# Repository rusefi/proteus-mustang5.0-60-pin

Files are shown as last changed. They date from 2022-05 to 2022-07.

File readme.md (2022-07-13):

Status: untested

See https://rusefi.com/forum/viewtopic.php?f=2&t=1890

[rev A schematics](https://github.com/rusefi/proteus-mustang5.0-60-pin/blob/main/boards/5.0mustangProteusPnP-a/board/5.0mustangProteusPnP-a-schematic.pdf)

[88 diagram](https://github.com/rusefi/rusefi/wiki/Ford-Fox-Body-(88-Ford-Mustang-302-V8))

# 5.0 Mustang Proteus PnP
PnP adapter board for 5.0 mustang EEC-IV computer using Proteus Rusefi v0.5 compatible board.

This board is designed as both a PnP stock replacement for the A9L/A9P EECs found in 5.0 manual foxbody mustangs, as well as a fully featured aftermarket ECU. This board is designed to fit into BOTH versions of the stock Ford EEC-IV case.

PLEASE do not rip apart any A9L computers to house this unit, there's very few of them left and they sell for a lot! Keep or sell that and buy any late 80s to early 90s EEC-IV as a donor instead such as 88 ford taurus 2.4 EEC for $25.

wiki and more info coming after fully tested.

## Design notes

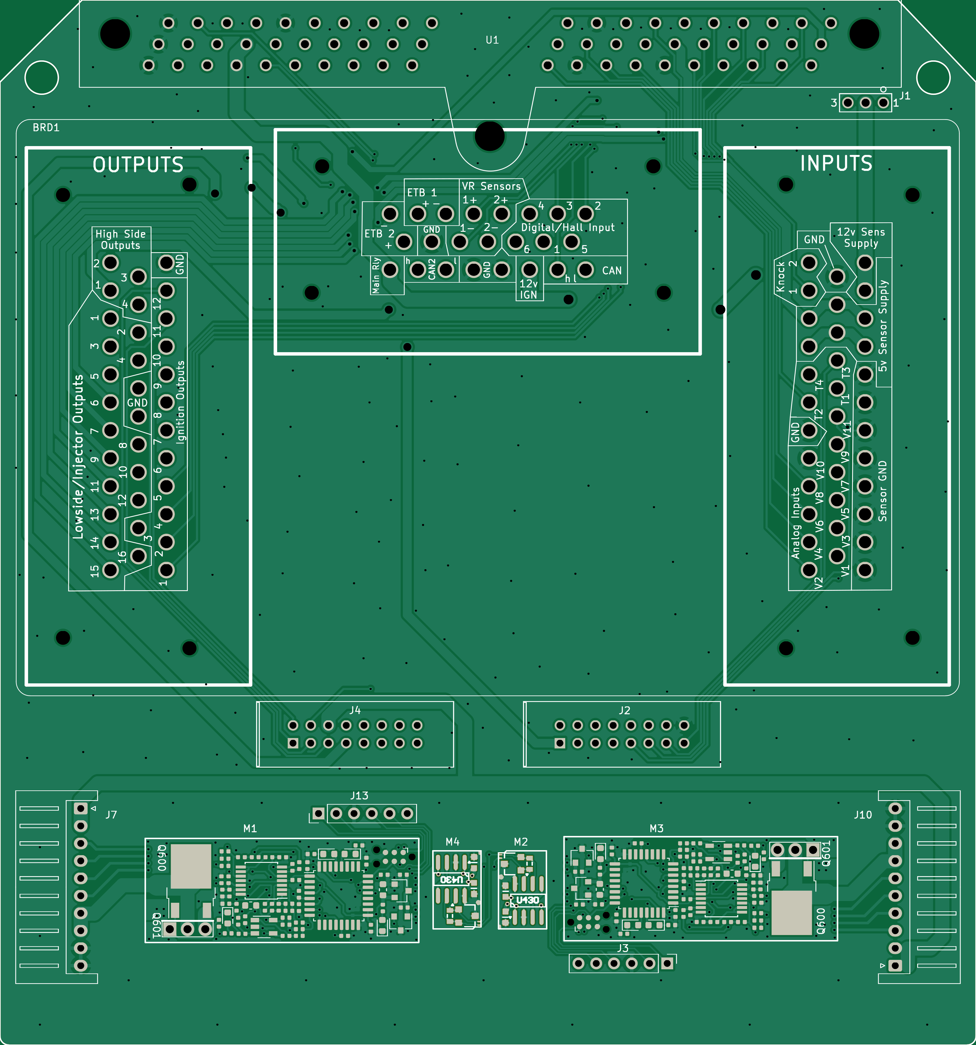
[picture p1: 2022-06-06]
boards/5.0mustangProteusPnP-a/board/misc/5.0mustangProteusPnP-a-top.png

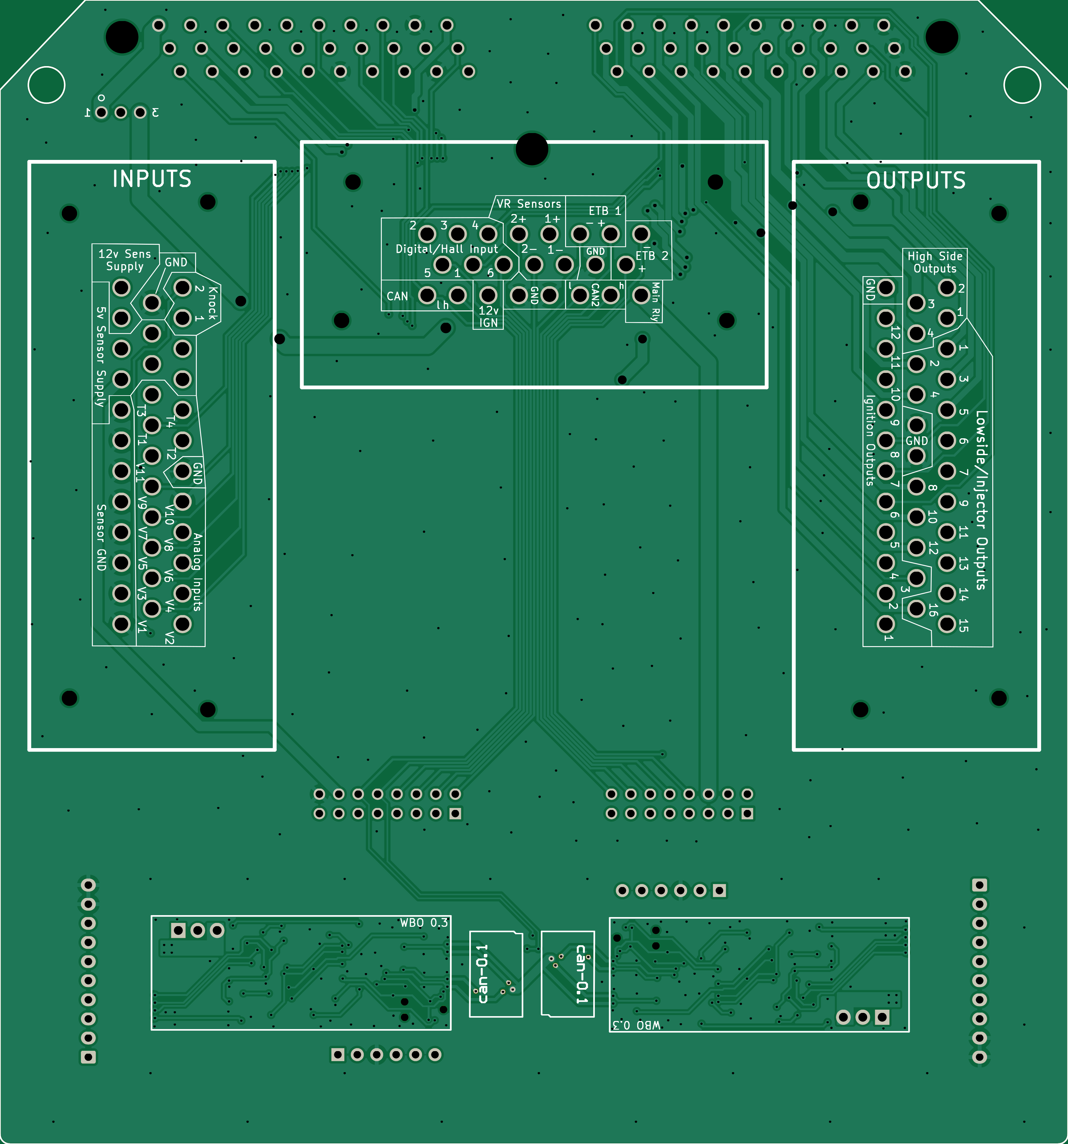
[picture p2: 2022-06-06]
boards/5.0mustangProteusPnP-a/board/misc/5.0mustangProteusPnP-a-bottom.png

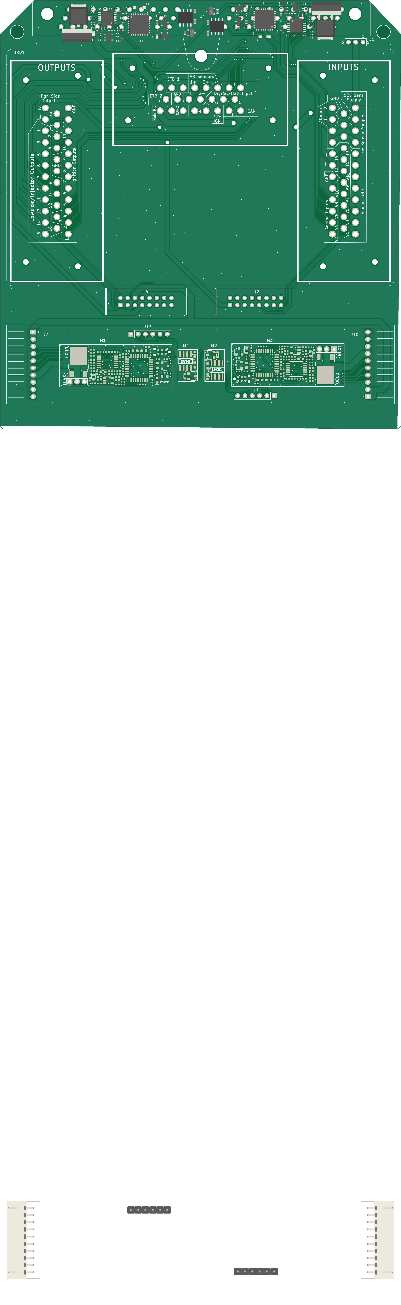
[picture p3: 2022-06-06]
boards/5.0mustangProteusPnP-a/board/5.0mustangProteusPnP-a.png

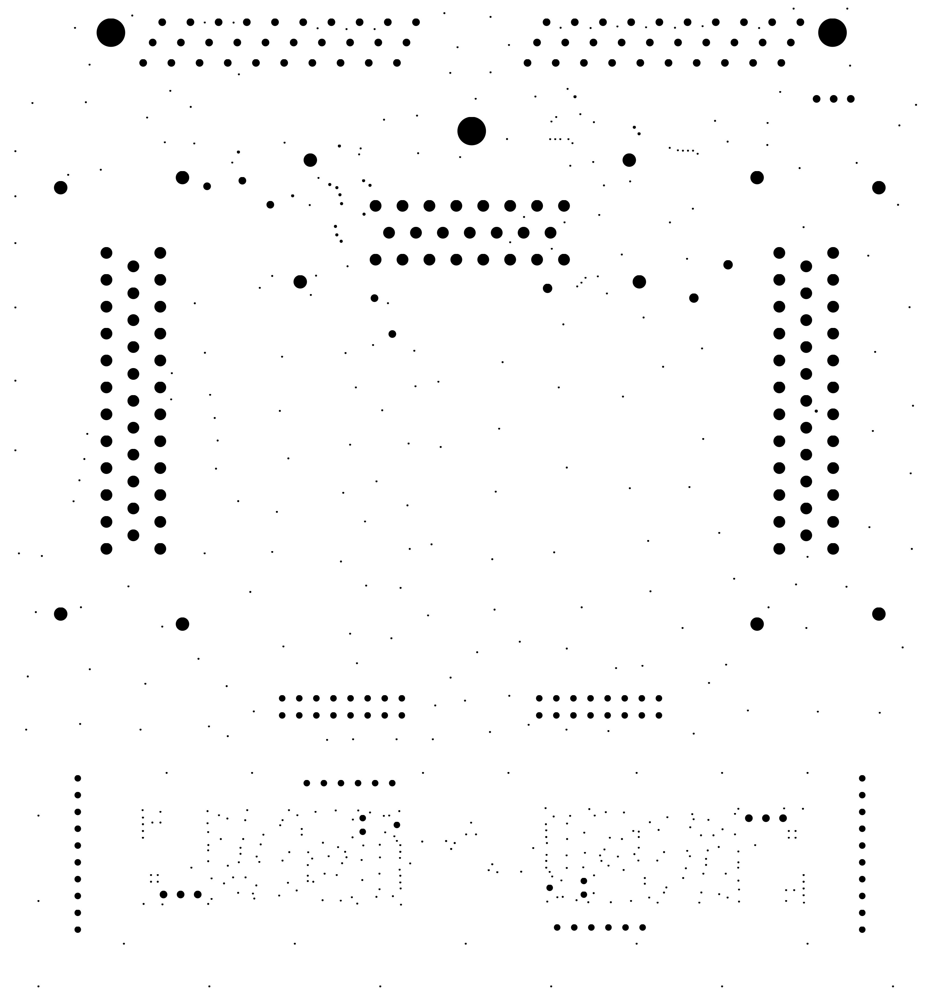
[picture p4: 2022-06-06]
boards/5.0mustangProteusPnP-a/board/misc/5.0mustangProteusPnP-a-outline.png

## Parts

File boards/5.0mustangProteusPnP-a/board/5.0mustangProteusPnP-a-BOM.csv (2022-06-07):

Comment | Designator | Footprint | LCSC Part #
proteus | BRD1 | proteus
5-146280-3 | J1 | 5-146280-3
5103308-3 | J2 | 5103308-3
Conn_01x06 | J3 | PinHeader_1x06_P2.54mm_Vertical
5103308-3 | J4 | 5103308-3
XH-10AW | J7, J10 | JST_XH_S10B-XH-A_1x10_P2.50mm_Horizontal | C14652
Conn_01x06 | J13 | PinHeader_1x06_P2.54mm_Vertical
FORD60PIN | U1 | FORD60PIN
1u | C600, C607, C609, C610, C611, C600_2, C607_2, C609_2, C610_2, C611_2 | C0402 | C52923
100n | C601, C602, C605, C608, C612, C613, C614, C615, C601_2, C602_2, C605_2, C608_2, C612_2, C613_2, C614_2, C615_2 | C0402 | C1525
33n | C603, C603_2 | C0402 | C1585
DNP | C604 | C0402
DNP | C606 | C0402
4.7u | C616, C616_2 | C0603 | C19666
LED-RED-0603 | D600, D603, D600_2, D603_2 | LED-0603 | C2286
LED-GREEN-0603 | D601, D601_2 | LED-0603 | C72043
LED-BLUE-0603 | D602, D602_2 | LED-0603 | C72041
BTS3028 | Q600, Q600_2 | DPAK | C112639
1k | R600, R601, R616, R617, R622, R626, R627, R628, R600_2, R601_2, R616_2, R617_2, R622_2, R626_2, R627_2, R628_2 | R0402 | C11702
68k | R602, R603, R602_2, R603_2 | R0402 | C36871
10k | R604, R605, R613, R614, R618, R619, R625, R604_2, R605_2, R613_2, R614_2, R618_2, R619_2, R625_2 | R0402 | C25744
10 | R606, R606_2 | R0402 | C25077
22k | R607, R607_2 | R0402 | C25768
47 | R608, R608_2 | R0402 | C25118
61.9 | R609, R609_2 | R0603 | C23092
20k | R610, R611, R612, R610_2, R611_2, R612_2 | R0402 | C25765
100k | R615, R621, R615_2, R621_2 | R0402 | C25741
27k | R620, R623, R620_2, R623_2 | R0402 | C25771
3.3k | R624, R624_2 | R0402 | C25890
MCP6004 | U600, U600_2 | TSSOP14 | C50282
STM32F042K6Tx | U602, U602_2 | LQFP32 | C69216
REF3033 | U603, U603_2 | SOT-23 | C36658
XC6206P332MR | U604, U604_2 | SOT-23 | C5446
100n | C430, C431, C430_2, C431_2 | C0603 | C14663
PESD1CAN | D430, D430_2 | SOT-23 | C343993
120 | R430, R430_2 | R0603 | C22787
TJA1051T/3/1J | U430, U430_2 | SO8 | C38695
DNP | C604_2 | C0402
DNP | C606_2 | C0402
GS8331-TR | U601, U601_2 | SOT-23-5 | C157712

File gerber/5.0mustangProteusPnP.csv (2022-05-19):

Comment | Designator | Footprint | LCSC Part #
proteus | BRD1 | Connector_Molex:proteus
5-146280-3 | J1 | 5-146280-3:5-146280-3
5103308-3 | J2 | 51033083:5103308-3
Conn_01x06 | J3 | Connector_PinHeader_2.54mm:PinHeader_1x06_P2.54mm_Vertical
5103308-3 | J4 | 51033083:5103308-3
XH-10AW | J7 | Connector_JST:JST_XH_S10B-XH-A_1x10_P2.50mm_Horizontal | C14652
XH-10AW | J10 | Connector_JST:JST_XH_S10B-XH-A_1x10_P2.50mm_Horizontal | C14652
Conn_01x06 | J13 | Connector_PinHeader_2.54mm:PinHeader_1x06_P2.54mm_Vertical
Module-wbo-0.3 | M1 | hellen-one-wbo-0.3:wbo
Module-can-0.1 | M2 | hellen-one-can-0.1:can
Module-wbo-0.3 | M3 | hellen-one-wbo-0.3:wbo
Module-can-0.1 | M4 | hellen-one-can-0.1:can
FORD60PIN | U1 | FORD60PIN:FORD60PIN

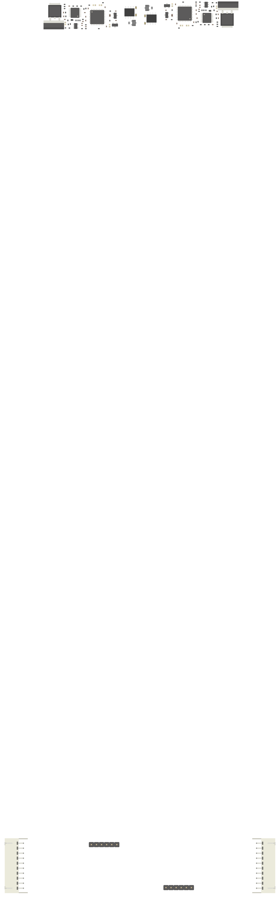
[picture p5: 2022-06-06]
boards/5.0mustangProteusPnP-a/board/misc/5.0mustangProteusPnP-a-components.png

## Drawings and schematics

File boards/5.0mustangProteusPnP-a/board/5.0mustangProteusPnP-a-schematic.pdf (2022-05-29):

# LS15(FAN) A12(1) HS3 A13(23) HS4 A14(22)

# LS4(INJ4) A16(20) GND A17(19) GND A18(18)

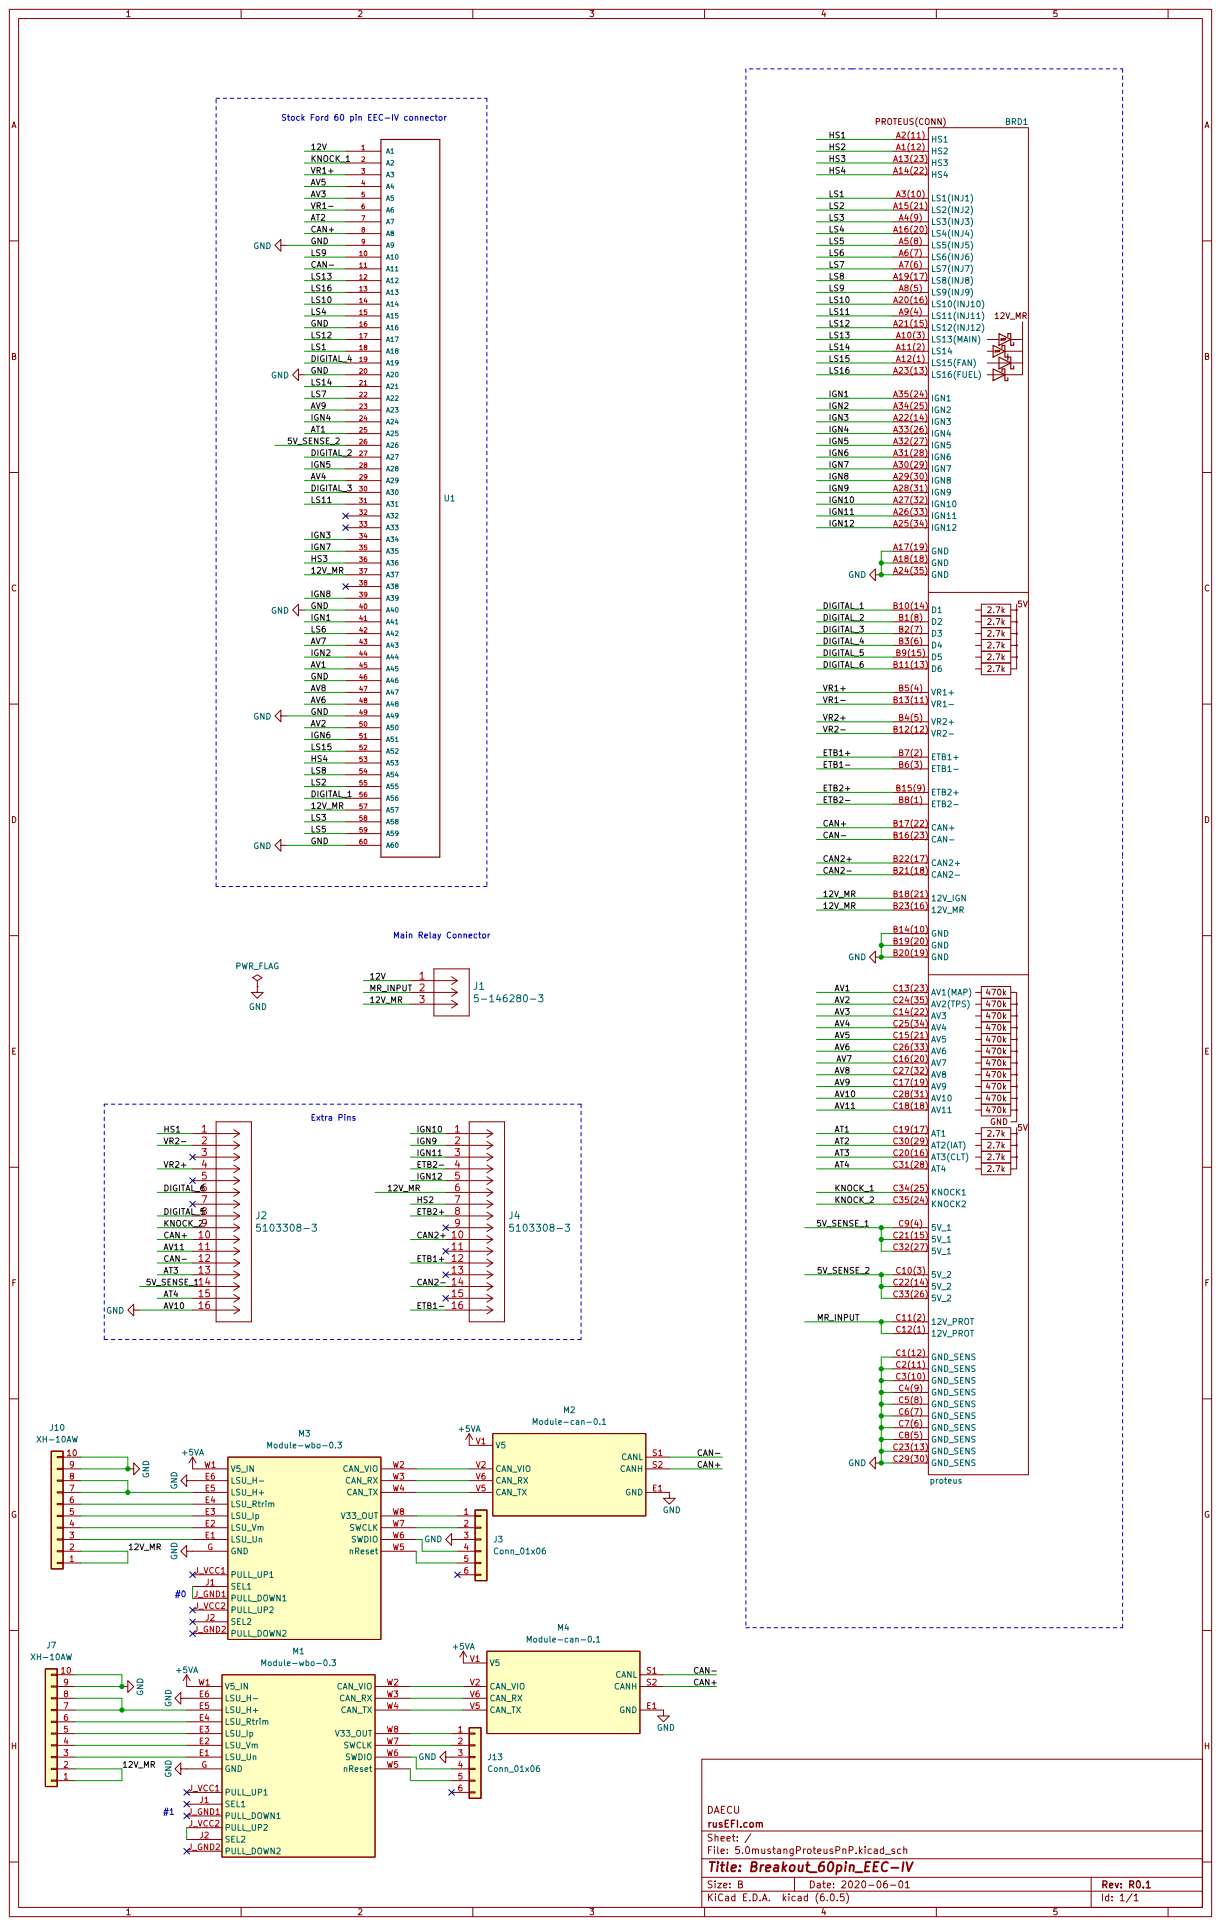
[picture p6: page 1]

IGN10 DIGITAL_2 Main Relay Connector Extra Pins

DAECU
File: 5.0mustangProteusPnP.kicad_sch Sheet: / rusEFI.com

1kR600

3.3k R623

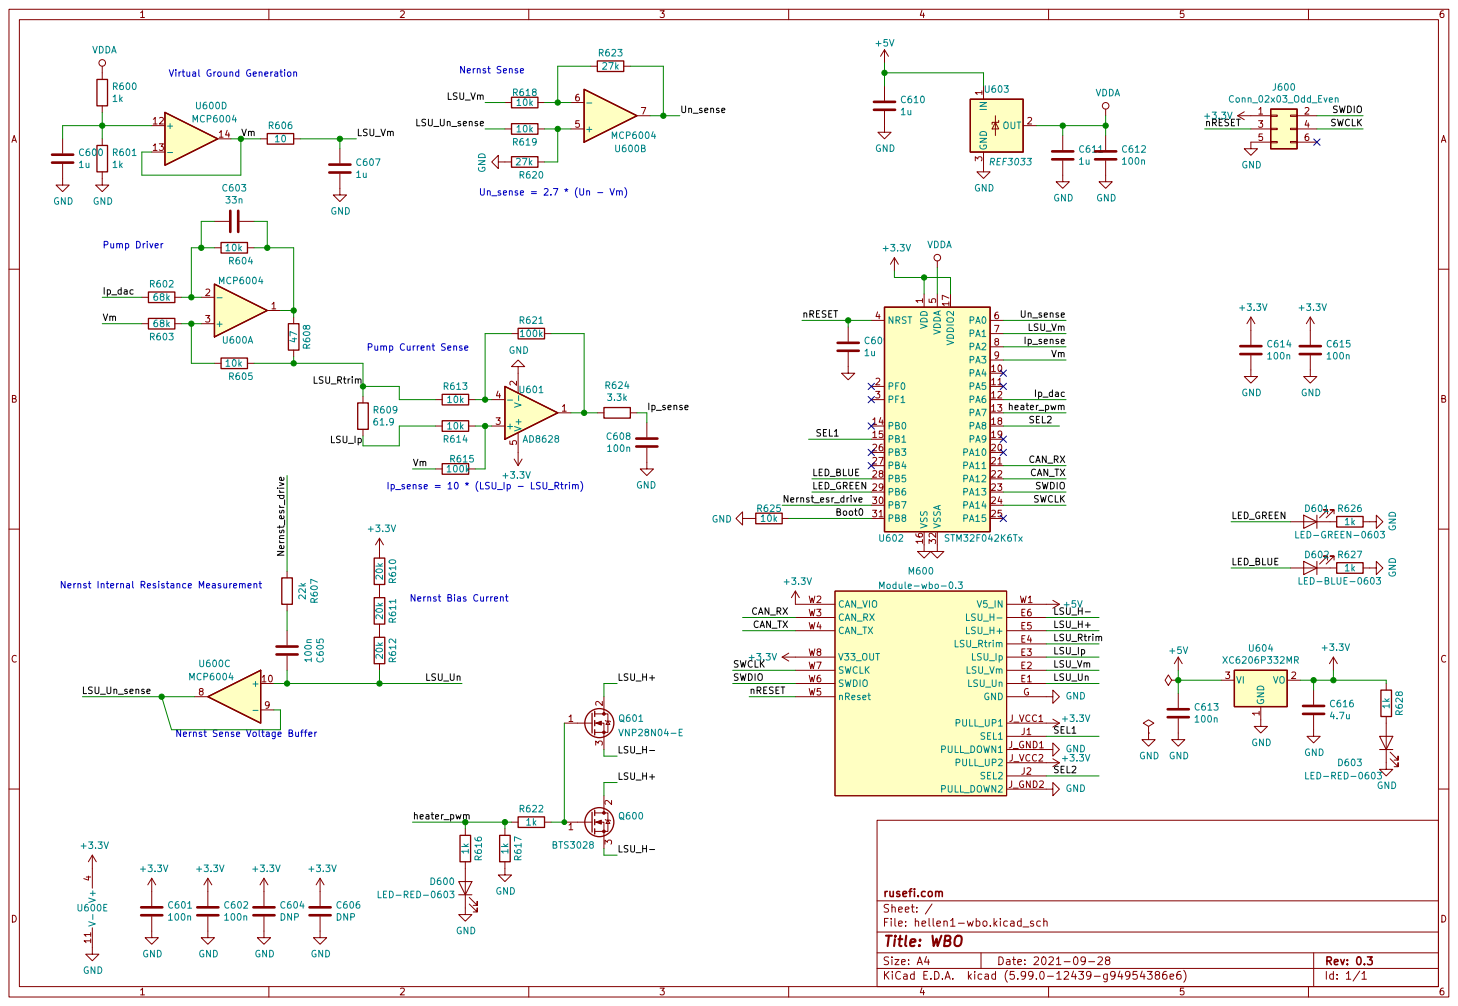
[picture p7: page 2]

Pump Current Sense Nernst Sense

LSU_Vm
Pump Driver Nernst Internal Resistance Measurement

1 VO 2 VI 3 U604 XC6206P332MR GND GND

1 PA4 10 PA5 11 PA6 12 PA7 13 PB0 14 PB1 15 VSS 16 VDDIO2 17 PA8 18 PA9 19 PF0 2 PA10 20 PA11 21 PA12 22 PA13 23 PA14 24 PA15 25 PB3 26 PB4 27 PB5 28 PB6 29 PF1 3 PB7 30 PB8 31 VSSA 32 NRST 4 VDDA

LED-RED-0603 ¹⁰⁰n C⁶⁰⁵ C604 DNP

Nernst Sense Voltage Buffer

1k GND GND R⁶¹⁶ ¹k

File: hellen1-wbo.kicad_sch Sheet: / rusefi.com

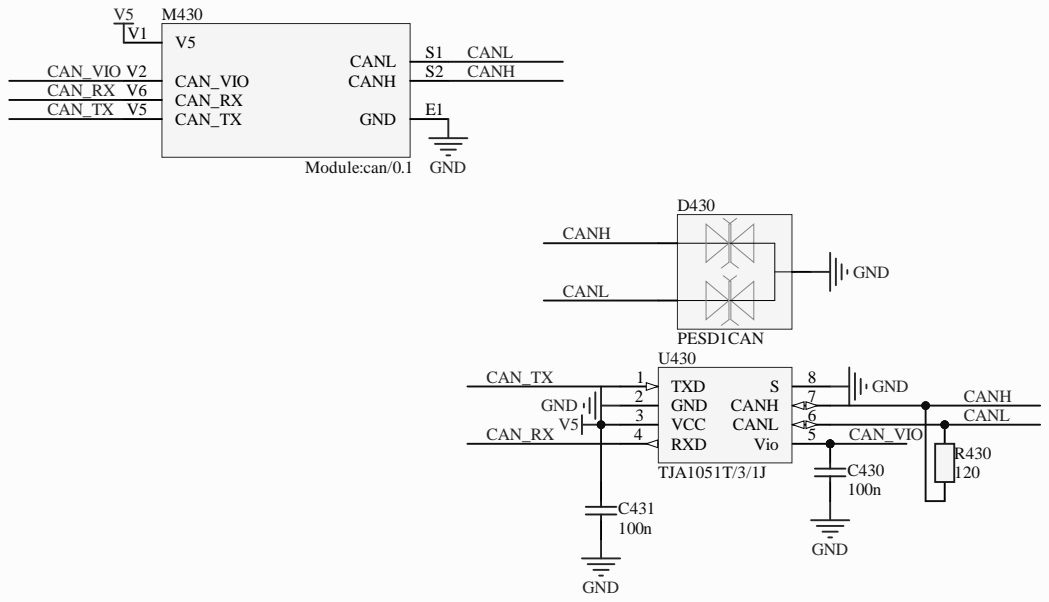
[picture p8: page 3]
andreika; Size:; Author:; Date:; Revision:; Sheet; PESD1CAN; GND; CANH; CANL; TXD 1 GND 2 VCC 3; Vio; 5 RXD 4; 6 CANH; TJA1051T/3/1J; CANH CANL; CAN_TX; CAN_RX; CAN_VIO; CAN_VIO V2; S2 CANL; CAN_TX V5; CAN_RX V6; Module:can/0.1

Hellen-One CAN
Title:

rusEFI EMS
Hellen-One Platform
https://rusefi.com/s/hellen72

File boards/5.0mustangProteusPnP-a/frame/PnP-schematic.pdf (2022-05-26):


IGN10 DIGITAL_2 Main Relay Connector Extra Pins

4 | LSU_Vm E2 | 2
3 | LSU_Un E1 | 3

DAECU
File: 5.0mustangProteusPnP.kicad_sch Sheet: / rusEFI.com

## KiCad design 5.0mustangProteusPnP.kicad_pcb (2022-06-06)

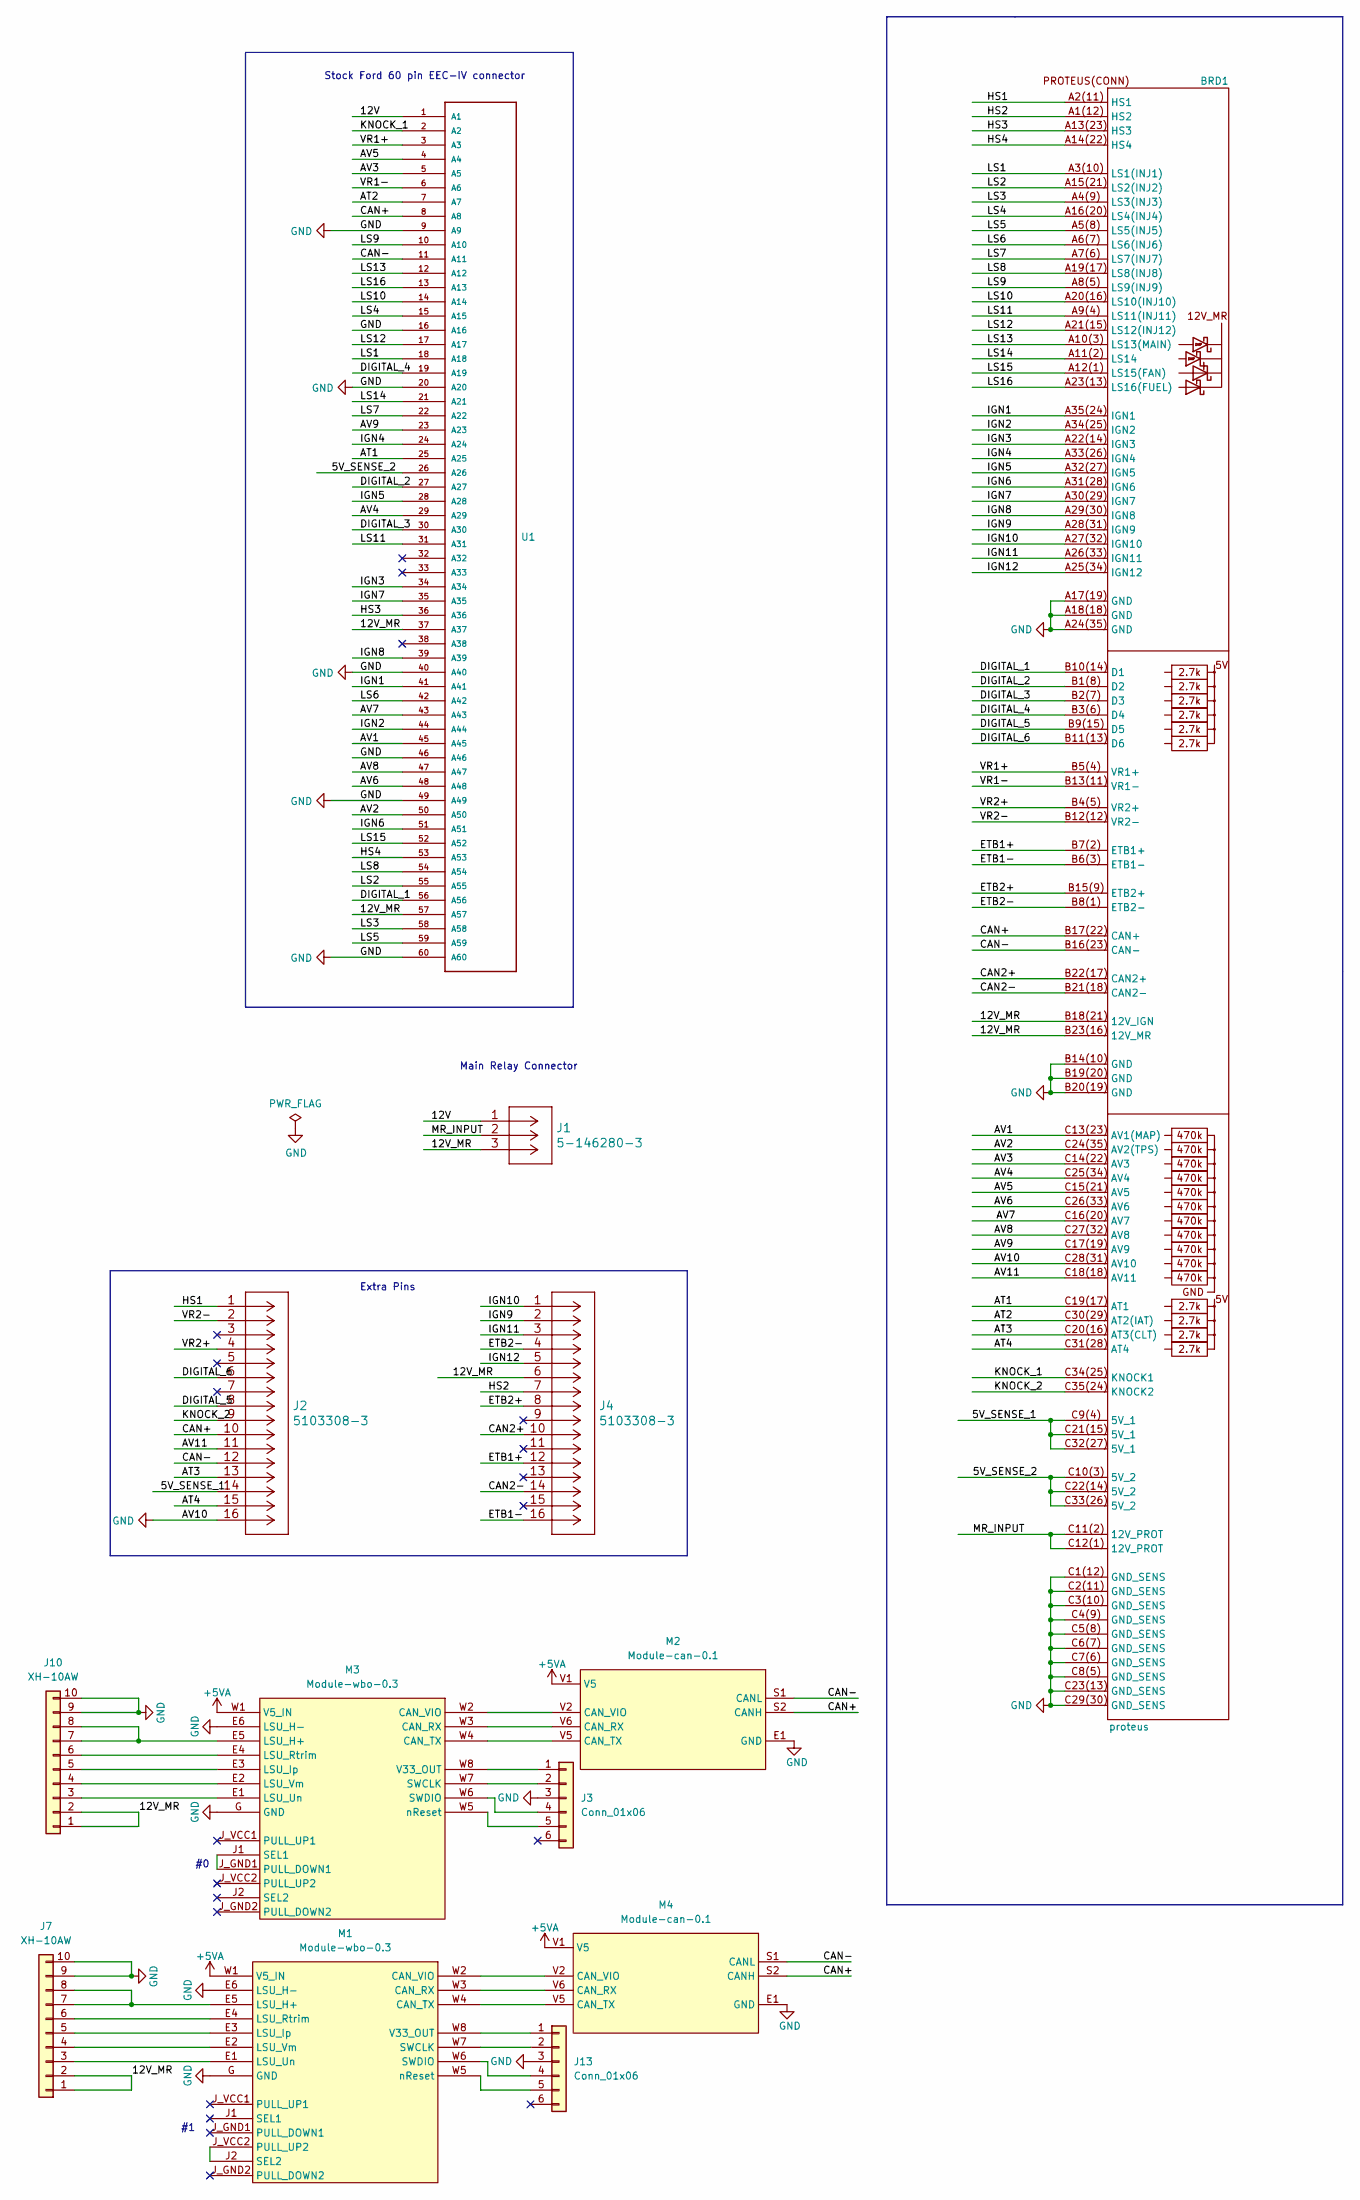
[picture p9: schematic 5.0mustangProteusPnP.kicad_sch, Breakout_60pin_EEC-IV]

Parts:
BRD1: proteus
J1: 5-146280-3
J2, J4: 5103308-3
J3, J13: Conn_01x06; PinHeader_1x06_P2.54mm_Vertical
J7, J10: XH-10AW; JST_XH_S10B-XH-A_1x10_P2.50mm_Horizontal; LCSC C14652
M1, M3: Module-wbo-0.3; wbo
M2, M4: Module-can-0.1; can
U1: FORD60PIN

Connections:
+5VA: M1.W1 (V5_IN), M2.V1 (V5), M3.W1 (V5_IN), M4.V1 (V5)
/5V_SENSE_1: BRD1.C9(4) (5V_1), BRD1.C21(15) (5V_1), BRD1.C32(27) (5V_1), J2.14
/5V_SENSE_2: BRD1.C10(3) (5V_2), BRD1.C22(14) (5V_2), BRD1.C33(26) (5V_2), U1.26 (A26)
/12V: J1.1, U1.1 (A1)
/12V_MR: BRD1.B18(21) (12V_IGN), BRD1.B23(16) (12V_MR), J1.3, J4.6, J7.1, J7.2, J10.1, J10.2, U1.37 (A37), U1.57 (A57)
/AT1: BRD1.C19(17) (AT1), U1.25 (A25)
/AT2: BRD1.C30(29) (AT2(IAT)), U1.7 (A7)
/AT3: BRD1.C20(16) (AT3(CLT)), J2.13
/AT4: BRD1.C31(28) (AT4), J2.15
/AV1: BRD1.C13(23) (AV1(MAP)), U1.45 (A45)
/AV2: BRD1.C24(35) (AV2(TPS)), U1.50 (A50)
/AV3: BRD1.C14(22) (AV3), U1.5 (A5)
/AV4: BRD1.C25(34) (AV4), U1.29 (A29)
/AV5: BRD1.C15(21) (AV5), U1.4 (A4)
/AV6: BRD1.C26(33) (AV6), U1.48 (A48)
/AV7: BRD1.C16(20) (AV7), U1.43 (A43)
/AV8: BRD1.C27(32) (AV8), U1.47 (A47)
/AV9: BRD1.C17(19) (AV9), U1.23 (A23)
/AV11: BRD1.C18(18) (AV11), J2.11
/CAN2+: BRD1.B22(17) (CAN2+), J4.10
/CAN2-: BRD1.B21(18) (CAN2-), J4.14
/CAN+: BRD1.B17(22) (CAN+), J2.10, M2.S2 (CANH), M4.S2 (CANH), U1.8 (A8)
/CAN-: BRD1.B16(23) (CAN-), J2.12, M2.S1 (CANL), M4.S1 (CANL), U1.11 (A11)
/DIGITAL_1: BRD1.B10(14) (D1), U1.56 (A56)
/DIGITAL_2: BRD1.B1(8) (D2), U1.27 (A27)
/DIGITAL_3: BRD1.B2(7) (D3), U1.30 (A30)
/DIGITAL_4: BRD1.B3(6) (D4), U1.19 (A19)
/DIGITAL_5: BRD1.B9(15) (D5), J2.8
/DIGITAL_6: BRD1.B11(13) (D6), J2.6
/ETB1+: BRD1.B7(2) (ETB1+), J4.12
/ETB1-: BRD1.B6(3) (ETB1-), J4.16
/ETB2+: BRD1.B15(9) (ETB2+), J4.8
/ETB2-: BRD1.B8(1) (ETB2-), J4.4
/HS1: BRD1.A2(11) (HS1), J2.1
/HS2: BRD1.A1(12) (HS2), J4.7
/HS3: BRD1.A13(23) (HS3), U1.36 (A36)
/HS4: BRD1.A14(22) (HS4), U1.53 (A53)
/IGN1: BRD1.A35(24) (IGN1), U1.41 (A41)
/IGN2: BRD1.A34(25) (IGN2), U1.44 (A44)
/IGN3: BRD1.A22(14) (IGN3), U1.34 (A34)
/IGN4: BRD1.A33(26) (IGN4), U1.24 (A24)
/IGN5: BRD1.A32(27) (IGN5), U1.28 (A28)
/IGN6: BRD1.A31(28) (IGN6), U1.51 (A51)
/IGN7: BRD1.A30(29) (IGN7), U1.35 (A35)
/IGN8: BRD1.A29(30) (IGN8), U1.39 (A39)
/IGN9: BRD1.A28(31) (IGN9), J4.2
/IGN10: BRD1.A27(32) (IGN10), J4.1
/IGN11: BRD1.A26(33) (IGN11), J4.3
/IGN12: BRD1.A25(34) (IGN12), J4.5
/KNOCK_1: BRD1.C34(25) (KNOCK1), U1.2 (A2)
/KNOCK_2: BRD1.C35(24) (KNOCK2), J2.9
/LS1: BRD1.A3(10) (LS1(INJ1)), U1.18 (A18)
/LS2: BRD1.A15(21) (LS2(INJ2)), U1.55 (A55)
/LS3: BRD1.A4(9) (LS3(INJ3)), U1.58 (A58)
/LS4: BRD1.A16(20) (LS4(INJ4)), U1.15 (A15)
/LS5: BRD1.A5(8) (LS5(INJ5)), U1.59 (A59)
/LS6: BRD1.A6(7) (LS6(INJ6)), U1.42 (A42)
/LS7: BRD1.A7(6) (LS7(INJ7)), U1.22 (A22)
/LS8: BRD1.A19(17) (LS8(INJ8)), U1.54 (A54)
/LS9: BRD1.A8(5) (LS9(INJ9)), U1.10 (A10)
/LS10: BRD1.A20(16) (LS10(INJ10)), U1.14 (A14)
/LS11: BRD1.A9(4) (LS11(INJ11)), U1.31 (A31)
/LS12: BRD1.A21(15) (LS12(INJ12)), U1.17 (A17)
/LS13: BRD1.A10(3) (LS13(MAIN)), U1.12 (A12)
/LS14: BRD1.A11(2) (LS14), U1.21 (A21)
/LS15: BRD1.A12(1) (LS15(FAN)), U1.52 (A52)
/LS16: BRD1.A23(13) (LS16(FUEL)), U1.13 (A13)
/MR_INPUT: BRD1.C11(2) (12V_PROT), BRD1.C12(1) (12V_PROT), J1.2
/VR1+: BRD1.B5(4) (VR1+), U1.3 (A3)
/VR1-: BRD1.B13(11) (VR1-), U1.6 (A6)
/VR2+: BRD1.B4(5) (VR2+), J2.4
/VR2-: BRD1.B12(12) (VR2-), J2.2
GND: BRD1.A17(19) (GND), BRD1.A18(18) (GND), BRD1.A24(35) (GND), BRD1.B14(10) (GND), BRD1.B19(20) (GND), BRD1.B20(19) (GND), BRD1.C1(12) (GND_SENS), BRD1.C2(11) (GND_SENS), BRD1.C3(10) (GND_SENS), BRD1.C4(9) (GND_SENS), BRD1.C5(8) (GND_SENS), BRD1.C6(7) (GND_SENS), BRD1.C7(6) (GND_SENS), BRD1.C8(5) (GND_SENS), BRD1.C23(13) (GND_SENS), BRD1.C28(31) (AV10), BRD1.C29(30) (GND_SENS), J2.16, J3.3, J7.9, J7.10, J10.9, J10.10, J13.3, M1.E6 (LSU_H-), M1.G (GND), M2.E1 (GND), M3.E6 (LSU_H-), M3.G (GND), M4.E1 (GND), U1.9 (A9), U1.16 (A16), U1.20 (A20), U1.40 (A40), U1.46 (A46), U1.49 (A49), U1.60 (A60)
unnamed: J3.1, M3.W8 (V33_OUT)
unnamed: J3.2, M3.W7 (SWCLK)
unnamed: J3.4, M3.W6 (SWDIO)
unnamed: J3.5, M3.W5 (nReset)
unnamed: J7.3, M1.E1 (LSU_Un)
unnamed: J7.4, M1.E2 (LSU_Vm)
unnamed: J7.5, M1.E3 (LSU_Ip)
unnamed: J7.6, M1.E4 (LSU_Rtrim)
unnamed: J7.7, J7.8, M1.E5 (LSU_H+)
unnamed: J10.3, M3.E1 (LSU_Un)
unnamed: J10.4, M3.E2 (LSU_Vm)
unnamed: J10.5, M3.E3 (LSU_Ip)
unnamed: J10.6, M3.E4 (LSU_Rtrim)
unnamed: J10.7, J10.8, M3.E5 (LSU_H+)
unnamed: J13.1, M1.W8 (V33_OUT)
unnamed: J13.2, M1.W7 (SWCLK)
unnamed: J13.4, M1.W6 (SWDIO)
unnamed: J13.5, M1.W5 (nReset)
unnamed: M1.J2 (SEL2), M1.J_VCC2 (PULL_UP2)
unnamed: M1.W2 (CAN_VIO), M4.V2 (CAN_VIO)
unnamed: M1.W3 (CAN_RX), M4.V6 (CAN_RX)
unnamed: M1.W4 (CAN_TX), M4.V5 (CAN_TX)
unnamed: M2.V2 (CAN_VIO), M3.W2 (CAN_VIO)
unnamed: M2.V5 (CAN_TX), M3.W4 (CAN_TX)
unnamed: M2.V6 (CAN_RX), M3.W3 (CAN_RX)
unnamed: M3.J1 (SEL1), M3.J_GND1 (PULL_DOWN1)

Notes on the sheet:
Stock Ford 60 pin EEC-IV connector
Extra Pins
Main Relay Connector

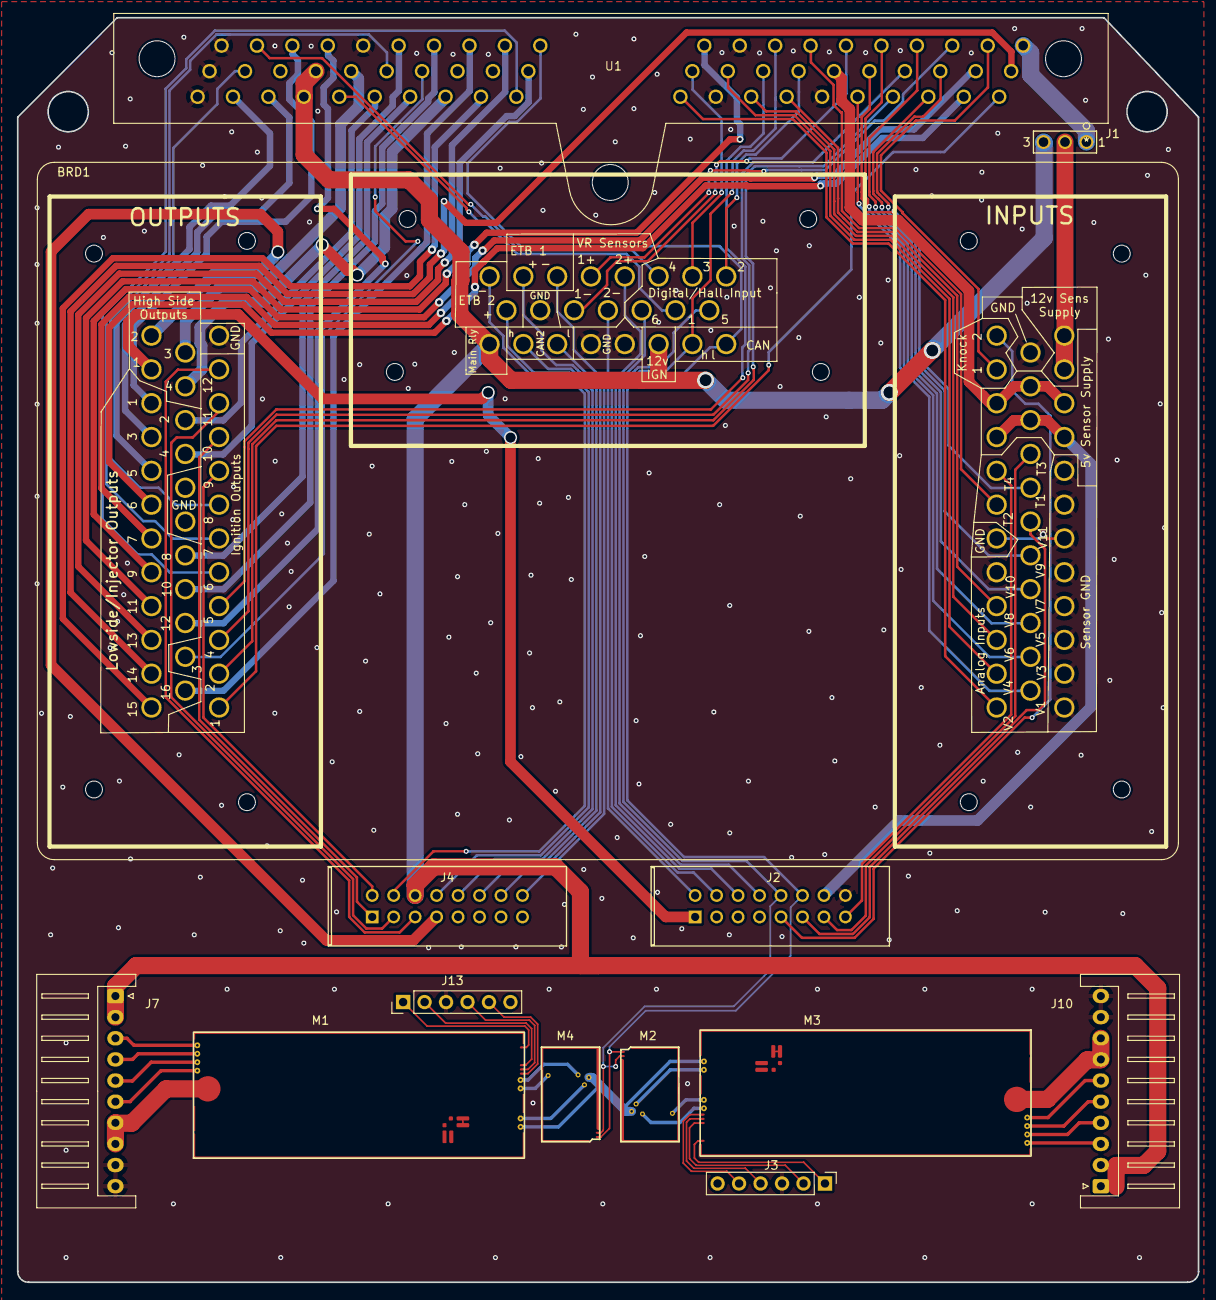
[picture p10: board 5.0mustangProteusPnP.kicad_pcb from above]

Board: 2 copper layers, 139.7 x 149.6 mm, 13 parts (0 on the bottom side), 99 nets.

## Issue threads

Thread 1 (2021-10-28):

migrate to KiCAD 6.0 and add dual WBO module

rusefillc, 2021-10-28:
in order to Hellen this board we would need to migrate to 5.99

Nadezhda-n, 2022-05-12:
Модуль нужно сделать как в примере (две одинаковые части) или на CAN и CAN2?

rusefillc, 2022-05-14:
Как в примере - оба модуля на одной и той же шине CAN

Closed 2022-05-14.

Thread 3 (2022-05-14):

Габариты

Nadezhda-n, 2022-05-14:
На плате заданы габариты 5.5 in * 6.5 in, при этом используется не все пространство (внизу пусто), мне туда и ставить модуль can или расширять?

rusefillc, 2022-05-15:
хороший вопрос! сегодня уточню, будем ли делать вот так:

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

rusefillc, 2022-05-15:
Давай сделаем как на моей картинке - повернём один на 180 градусов и увеличим плату снизу?

Nadezhda-n, 2022-05-15:
А что за линии снищу, будто она уже увеличена?
Мне это игнорировать?

rusefillc, 2022-05-15:
не понимаю про линии. идея в том, чтоб увеличить снизу в разумных объёмах - без кучи лишнего свободного места

Closed 2022-05-17.

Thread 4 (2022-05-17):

Название, лого, версия

Nadezhda-n, 2022-05-17:
Вероятно все или что-то из этого надо поменять/нарисовать на плате

rusefillc, 2022-05-17:
автора оставим
адрес
https://github.com/rusefi/proteus-mustang5.0-60-pin
версия
"V0.2re"

Closed 2022-05-19.

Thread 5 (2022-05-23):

Экспорт по инструкции

rusefillc, 2022-05-23:
Экспорт точно был сделан не по инструкции - инструкция говорит имя папки "geber", а экспорт был в другую папку

инструкция https://github.com/andreika-git/hellen-one/wiki/kicad-export-frame

это важно, потому что почему-то необычно не склеиваются платы https://github.com/rusefi/proteus-mustang5.0-60-pin/runs/6560512669?check_suite_focus=true

предлагаю сделать новый экспорт более точно по инструкции и посмотреть, поменяется ли красная иконка на зелёную в https://github.com/rusefi/proteus-mustang5.0-60-pin/commits/main

Closed 2022-05-26.

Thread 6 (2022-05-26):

need help

rusefillc, 2022-05-26:
even with #5 create board step has failed

@andreika-git please advice

andreika-git, 2022-05-26:
Maybe this one would help?
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

rusefillc, 2022-05-26:
@Nadezhda-n please adjust ^^^. Возможно нужно будет подвинуть origin marker, чтоб всё было в положительной области

и новый экспорт по той же инструкции плиз.

Nadezhda-n, 2022-05-26:
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

Nadezhda-n, 2022-05-26:
@andreika-git
Это может быть из-за того, что точка начала координат стала с отрицательной коррдинатой (в абсолюте)?
Больше ничего не менялось

andreika-git, 2022-05-27:
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

The 'hellen-one' submodule has been changed in the latest commit. Currently it points to the "Apr,14" version (which is really old). Please revert it and use only the latest version of hellen-one.

rusefillc, 2022-05-27:
@andreika-git я вернул hellen-one новейший, но всё равно не работает

Nadezhda-n, 2022-05-29:
Все же сдвинула всю плату в положительную область

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

Closed 2022-06-02.

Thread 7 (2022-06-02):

modules are offset both on preview and gerbers

rusefillc, 2022-06-02:
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

rusefillc, 2022-06-02:
@andreika-git need your advice here, what have we missed?

Is any validation of this issue possible? Would it be trivial or not?

andreika-git, 2022-06-02:
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

1) Check the outline of the frame ("Edge.Cuts" should contain the closed line shape)
2) Check the "origin" - it should match the coordinates of the left bottom corner of the frame outline

Nadezhda-n, 2022-06-06:
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

andreika-git, 2022-06-06:
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

This is not origin. The origin is not set!

That's the origin (the red one):

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

As I already told you, you must set the origin:

Nadezhda-n, 2022-06-06:
Для меня это сейчас стало открытием, спасибо.
Дело именно в этом.
Чуть позже исправлю

Closed 2022-06-06.

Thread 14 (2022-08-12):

Drew reports issues with TPS and fuel pump

rusefillc, 2022-08-12:
See https://rusefi.com/forum/viewtopic.php?p=46047#p46047

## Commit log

2022-05-12 update
    обновила до 6.0, поставила современный футпринт
    [5.0mustangProteusPnP.kicad_pcb, 5.0mustangProteusPnP.kicad_sch, 5.0mustangProteusPnP.sch]
2022-05-15 add WBO module in sch
    [5.0mustangProteusPnP.kicad_pcb, 5.0mustangProteusPnP.kicad_sch]
2022-05-17 трассировка
    [5.0mustangProteusPnP.kicad_pcb, 5.0mustangProteusPnP.kicad_sch]
2022-05-19 add export files
    [5.0mustangProteusPnP-B_Cu.gbl, 5.0mustangProteusPnP-B_Mask.gbs, 5.0mustangProteusPnP-B_Silkscreen.gbo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]
2022-05-23 proper folder name
    [5.0mustangProteusPnP-B_Cu.gbl, 5.0mustangProteusPnP-B_Mask.gbs, 5.0mustangProteusPnP-B_SilkS.gbo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]
2022-05-23 proper folder name x2
    [5.0mustangProteusPnP-B_Cu.gbl, 5.0mustangProteusPnP-B_Mask.gbs, 5.0mustangProteusPnP-B_Silkscreen.gbo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]
2022-05-26 new outputs
    [5.0mustangProteusPnP-B_Cu.gbl, 5.0mustangProteusPnP-B_Mask.gbs, 5.0mustangProteusPnP-B_Silkscreen.gbo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]
2022-05-26 axes
    изменила направление отчета по оси ординат
    [5.0mustangProteusPnP-B_Cu.gbl, 5.0mustangProteusPnP-B_Mask.gbs, 5.0mustangProteusPnP-B_Silkscreen.gbo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]
2022-05-29 new gerbers
    [5.0mustangProteusPnP-B_Cu.gbl, 5.0mustangProteusPnP-B_Mask.gbs, 5.0mustangProteusPnP-B_Silkscreen.gbo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]
2022-05-29 Auto-generated board
    [5.0mustangProteusPnP-a-BOM.csv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]
2022-06-06 я пробую свои теории
    с абсолютным началом
    [5.0mustangProteusPnP-B_Cu.gbl, 5.0mustangProteusPnP-B_Mask.gbs, 5.0mustangProteusPnP-B_Silkscreen.gbo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]
2022-06-06 new gerbes
    Эта ревизия с проставленным началом координат. Странная конечно прога, имеющая три свои сетки одновременно :)
    [5.0mustangProteusPnP-B_Cu.gbl, 5.0mustangProteusPnP-B_Mask.gbs, 5.0mustangProteusPnP-B_Silkscreen.gbo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]
2022-06-06 size board
2022-06-07 replace progress
    [bom_replace_5.0mustangProteusPnP-a.csv]

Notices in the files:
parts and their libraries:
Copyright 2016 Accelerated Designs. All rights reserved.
